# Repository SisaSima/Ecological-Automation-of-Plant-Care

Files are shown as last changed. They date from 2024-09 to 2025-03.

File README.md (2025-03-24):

# Ecological-Automation-of-Plant-Care

We are currently facing many environmental challenges, such as global warming and water scarcity, which pose great challenges for effective sustainable plant cultivation. Traditional methods of irrigation and care often lead to insufficient watering or, conversely, to overflowing the plants, which not only wastes water, but can also cause soil rot, which can later appear on the products.

 In the future, an innovative solution to these problems may be ecological automation of plant care, which combines automated irrigation based on learning and recycling of excess water.

 The main goal of the work is to create an automated system that monitors and controls soil irrigation, while responding to environmental factors such as air humidity and ambient temperature. An important part of the project is also efficient water management through its recycling. Excess water is captured, filtered and reused, which significantly contributes to reducing consumption and promotes sustainability.

 This work describes in detail the individual steps of the development of this device from the design to the implementation of sensors and learning algorithms.

DSCF5349

# Hardware
Circut diagram and PCB were made in KiCAD.

Used electroparts:
- Raspberry pi Pico W - https://techfun.sk/produkt/raspberry-pi-pico-w/
- SHT30 - https://techfun.sk/produkt/senzor-teploty-a-vlhkosti-vzduchu-sht30/
- Capacitive Soil Humidity sensor - https://techfun.sk/produkt/kapacitny-senzor-vlhkosti-pody/
- OLED 1.3" display 128x64 - https://techfun.sk/produkt/oled-1-3-display-128x64/
- Water Level sensor (homemade)
- Small Water Pump - https://techfun.sk/produkt/mala-vodna-pumpa/
- Battery 5V
- Charging Module - https://techfun.sk/produkt/nabijaci-modul-pre-litiove-baterie-tp4056-ochranny-obvod-rozne-typy/

### Diagram


### PCB


# Code
 To run the code on the Raspberry pi Pico W, you need to install circuitpython on it. Detailed instructions for its installation can be found [here](https://learn.adafruit.com/welcome-to-circuitpython/installing-circuitpython).

Then you just transfer the files from the code folder to the device. In order for the programs to run, it is necessary to move the "lib" folder, in which all used libraries are stored, to the device.

To immediately, automatically start the program after starting, it is necessary to name the required file "code.py" (this step is already done). IN the folder there are wro versions of "code.py" file:
- code.py
- code_no_LA.py

"code_no_LA.py" has no Learning algorithm implemented and it's used just for testing functionnality od circuit and program. On the other hand code.py has already implemented algorithms and is used as a final version of code.

### Algorithm
As I mentioned, this project is powered by learning algorithm used to find the perfect amout of water to irrigate the soil. This operation is done by calculating difference between wanted soil moisture and the one we got by irrigating. the difference is than used to enlenght or enshort the time of irrigation.
```python
doba_polievania = doba_polievania*(chcena_val/(moisture_level*(120/100)))
```
The resulting value is then saved to a file in the SD card and then used in the next cycle as the watering time. The same way is stored the value of soil moisture after watering, so that it is then possible to create a graph comparing these two values

### Dataread
In order to better navigate the collected data, I programmed the code that creates a graph from it.
You can find the program and its user manual in the "dataread" folder.

The result should look like this:

test_graf

# 3D Model
 I shared a 'box_model.3mf' file, ready to be printed on 3d printer. The model should look like this:



 There is a place left for the battery and charging module. I personally filled the hole with memory foam and powered it directly with micro USB-B (connected to Raspberry pi Pico W).
#### WARNING! UPPER HOLE FOR USB CABLE is too small. You can enlarge it in any 3D modeling program. In case you are not able to do that, you can use a drill.

logoEAoPCsmol

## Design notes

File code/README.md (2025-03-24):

To run the code, it has to have name "code.py". 

There are two versions of the code: "code.py" and "code_no_LA.py":

"code.py" is based on the comparison of two values - "dry_val" and the actual soil moisture value. When the actual soil moisture value is less than the minimum allowed value (dry_val), the soil will be automatically irrigated until the moisture value is greater than dry_val

"code_no_LA.py" uses a simple machine learning model that learns how long to water the plant so that its final soil moisture value is the same as a pre-defined desired value - "chcena_val"

In the "sensor test" folder there are codes for testing the functionality of individual sensors

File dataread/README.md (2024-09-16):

#### To run the program, it is necessary to download the "matplotlib" package. ([here](https://matplotlib.org/stable/install/index.html))

### Instructions to use:
- Insert the files "doba_polievania.txt" and "vlhkost.txt" into the folder
- run the program using the followinf code:
```python
python main.py
```

The result should look like this:

test_graf

orange is for soil humidity and blue for watering time

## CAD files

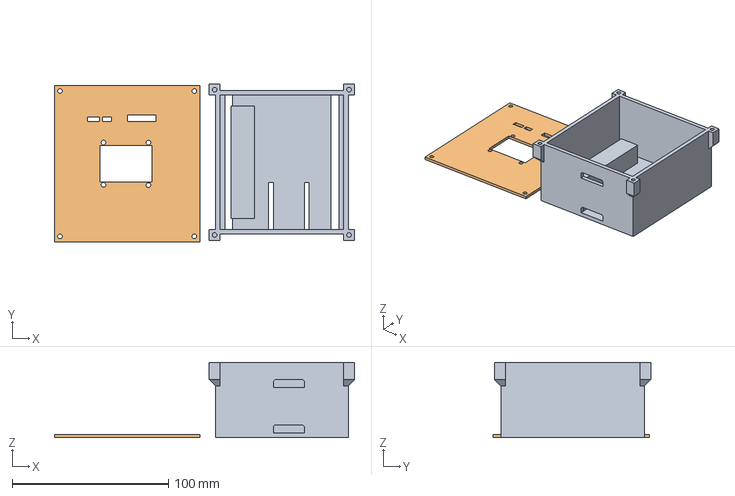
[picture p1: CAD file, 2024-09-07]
box_model.3mf
192.0 x 100.9 x 48.0 mm

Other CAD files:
box_model.f3d

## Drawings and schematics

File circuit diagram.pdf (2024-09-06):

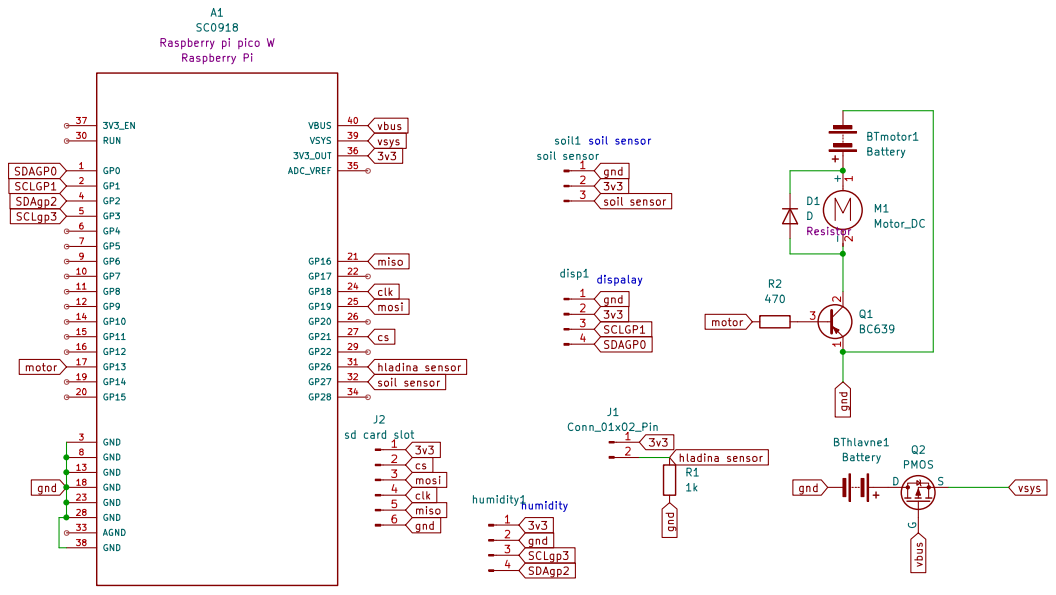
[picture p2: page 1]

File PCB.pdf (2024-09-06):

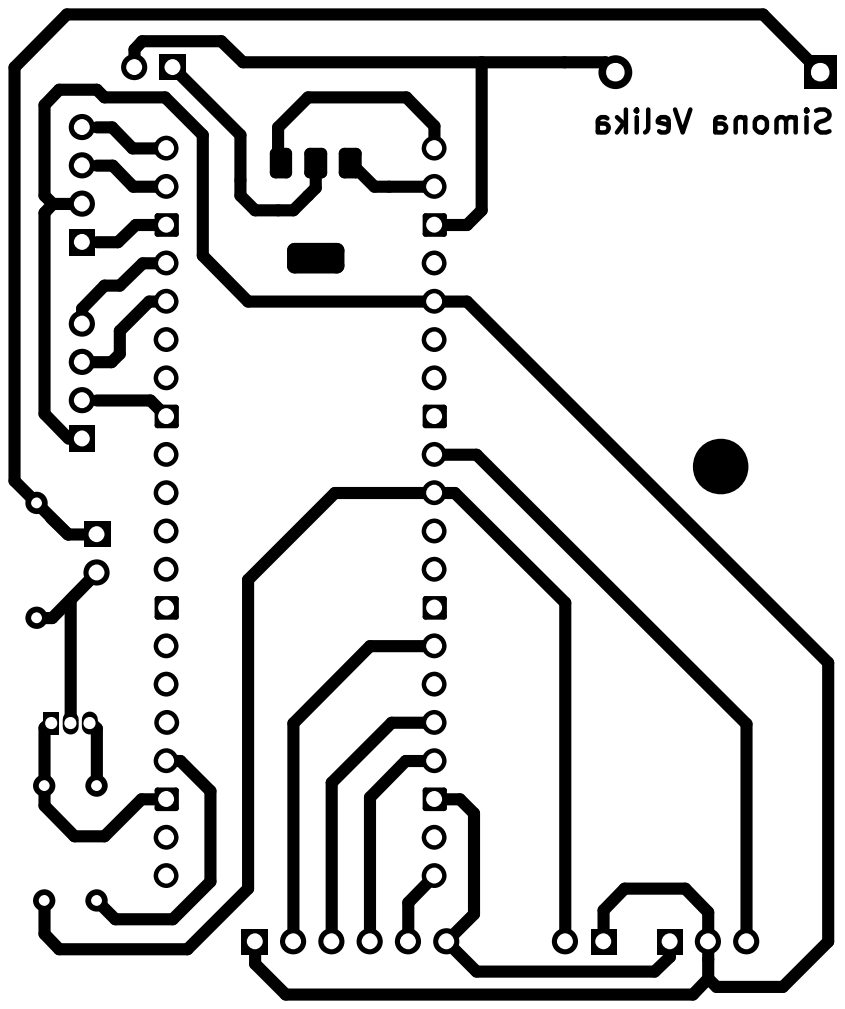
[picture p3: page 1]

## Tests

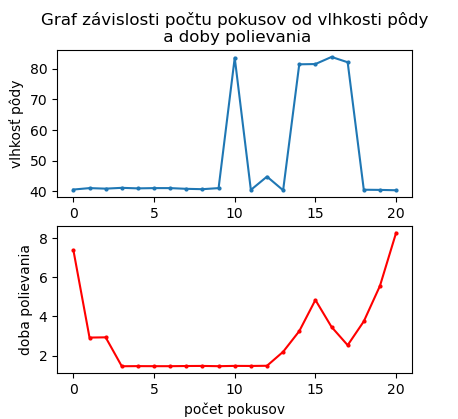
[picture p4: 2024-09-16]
dataread/test_graf.png

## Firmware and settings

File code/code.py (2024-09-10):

import time
import board
from analogio import AnalogIn
import digitalio
import busio
import displayio
import terminalio
from adafruit_display_text import label
from adafruit_displayio_sh1106 import SH1106
from digitalio import DigitalInOut, Direction, Pull
import adafruit_sht31d
import adafruit_sdcard
import storage


# premenne
doba_polievania = float(5)
cas_kontroly = 0.1
dry_val = 45
chcena_val = 60 # pozadovana vlhkost
filename = "doba_polievania"
filename2 = "vlhkost"
odmlka_senzoru = 5

   

# výška hladiny premenne
malo = 0.35
polovica = 0.56
akurat = 0.7
full = 0.85
error = 1.5

#SDcard
# Initialize SPI bus and pins
spi = busio.SPI(board.GP18, MOSI=board.GP19, MISO=board.GP16)
cs = digitalio.DigitalInOut(board.GP21)  # Chip select pin (pin 7)
# Initialize SD card object
sdcard = adafruit_sdcard.SDCard(spi, cs)
# Mount the SD card
vfs = storage.VfsFat(sdcard)
storage.mount(vfs, "/sd")
# Create a file and write data to it

try:
    with open("/sd/{0}.txt".format(filename), "r") as file:
        for line in file:
            pass
        doba_polievania = float(line)
        print(doba_polievania)
except:
    doba_polievania = doba_polievania


"""
THIS WORKS
with open("/sd/{0}.txt".format(filename), "a") as file:
    file.write("\n{0}".format(doba_polievania))
with open("/sd/{0}.txt".format(filename), "r") as file:
    for line in file:
        pass
    doba_polievania = line
    print(doba_polievania)
"""

# SHT30
i2c_sht30 = busio.I2C(scl=board.GP3, sda=board.GP2)
sensor = adafruit_sht31d.SHT31D(i2c_sht30)

# moturek definice
moturek = digitalio.DigitalInOut(board.GP13)
moturek.direction = digitalio.Direction.OUTPUT

# Display
displayio.release_displays()
sda_pin = board.GP0
scl_pin = board.GP1
i2c = busio.I2C(scl=scl_pin, sda=sda_pin)
display_bus = displayio.I2CDisplay(i2c, device_address=0x3C)
WIDTH = 130
HEIGHT = 70
display = SH1106(display_bus, width=WIDTH, height=HEIGHT, rotation=180)
display.auto_refresh = False
splash = displayio.Group()
display.show(splash)
# Draw a label
text = ""
text_area = label.Label(terminalio.FONT, text=text, color=0xFFFF00, x=2, y=10)
splash.append(text_area)

# soil moisture
soil_moisture_pin = AnalogIn(board.A1)
#hladina vody
hladina_vody_pin = AnalogIn(board.A0)


def get_voltage(pin):
    return (pin.value * 3.3) / 65536
def get_moisture_level(voltage):
    return 100-(voltage / 3.3)*100
    #return voltage/3.3


while True:

    print(doba_polievania)
    
    temperature = sensor.temperature
    humidity = sensor.relative_humidity
    print(f"Temperature: {temperature:.2f} C")
    print(f"Humidity: {humidity:.2f} %")
    
# Read the voltage from the soil moisture sensor
    voltage = get_voltage(soil_moisture_pin)
    voltage_hladina_vody = get_voltage(hladina_vody_pin)
    
# hodnoty výšky hladiny vody
    if voltage_hladina_vody <= malo:
        voltage_hladina_vody_value = 'malo'
    if voltage_hladina_vody <= polovica and voltage_hladina_vody >= malo:
        voltage_hladina_vody_value = 'polovica'
    if voltage_hladina_vody <= akurat and voltage_hladina_vody >= polovica:
        voltage_hladina_vody_value = 'akurat'
    if voltage_hladina_vody >= akurat and voltage_hladina_vody <= full:
        voltage_hladina_vody_value = 'full'
    if voltage_hladina_vody >= full:
        voltage_hladina_vody_value = 'error:touching'

# Calculate the moisture level percentage
    moisture_level = get_moisture_level(voltage)
    
    # Print the values
    #print("Soil Moisture Voltage: {:.2f} V".format(voltage))
    print("Soil Moisture Level: {:.2f}%".format(moisture_level*(120/100)))
    
    print()
    
    text_area.text = "soil:{0}\nhladina:{1}\nteplota:{2}\nvlhkost:{3}".format(moisture_level*(120/100),voltage_hladina_vody_value, temperature, humidity)
    display.refresh()

    if moisture_level*(120/100) <= dry_val:
        print('moturek on')
        moturek.value = True
        time.sleep(doba_polievania)
        moturek.value = False
        time.sleep(odmlka_senzoru)

        # znovu zneram hodnotu na moisture analog pine, aby som zistila novú hodnotu
        voltage = get_voltage(soil_moisture_pin)
        moisture_level = get_moisture_level(voltage)
        with open("/sd/{0}.txt".format(filename2), "a") as file:
            file.write("\n{0}".format(moisture_level*(120/100)))

        # algoritmus
        doba_polievania = doba_polievania*(chcena_val/(moisture_level*(120/100)))
        with open("/sd/{0}.txt".format(filename), "a") as file:
            file.write("\n{0}".format(doba_polievania))

        # display refresh
        text_area.text = "soil:{0} Motor on\nhladina:{1}\nteplota:{2}\nvlhkost:{3}".format(moisture_level*(120/100),voltage_hladina_vody_value, temperature, humidity)
        display.refresh() 
        
        text_area.text = "soil:{0} Motor on\nhladina:{1}\nteplota:{2}\nvlhkost:{3}".format(moisture_level*(120/100),voltage_hladina_vody_value, temperature, humidity)
        display.refresh()        
        #time.sleep(doba_polievania)

    else:
        print('moturek off')
        moturek.value = False
        text_area.text = "soil:{0}\nhladina:{1}\nteplota:{2}\nvlhkost:{3}".format(moisture_level*(120/100),voltage_hladina_vody_value, temperature, humidity)
        display.refresh()        

# new doba_polievania value check
    try:
        with open("/sd/{0}.txt".format(filename), "r") as file:
            for line in file:
                pass
            doba_polievania = float(line)
            print(doba_polievania)
    except:
        doba_polievania = doba_polievania
     
    time.sleep(cas_kontroly)

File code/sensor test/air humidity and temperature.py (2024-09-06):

import time
import board
import busio
import adafruit_sht31d

# Create I2C bus
i2c = busio.I2C(scl=board.GP3, sda=board.GP2)

# Create sensor instance
sensor = adafruit_sht31d.SHT31D(i2c)

# Main loop to read temperature and humidity
while True:
    temperature = sensor.temperature
    humidity = sensor.relative_humidity

    print(f"Temperature: {temperature:.2f} C")
    print(f"Humidity: {humidity:.2f} %")

    time.sleep(0.1)  # Delay for 2 seconds
